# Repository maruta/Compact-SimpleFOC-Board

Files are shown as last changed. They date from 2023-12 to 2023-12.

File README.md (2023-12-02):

# Compact SimpleFOC Controller Board

This repository contains design data for a BLDC motor controller board composed of:

* RP2040 (Controller)
* TMC6300 (Driver)
* MT6535 (Magnetic Angle Sensor)
* INA240 (Current Sense Amplifier)

and mainly designed for a tiny inverted pendulm project.

Wheeled inverted pendulum powered by SimpleFOC-1080p60H mov (https://youtu.be/5sXEKwi0VvQ?si=sFahMU4BhdU_3RiM)

## Disclaimer

The information and design files in this repository are provided "as is" without warranty of any kind, express or implied. We make no guarantees regarding the functionality or reliability of these designs. Users assume full responsibility for the application and use of these files. Any commercial application of these designs is at the user's own risk.

## Description

The board is designed primarily for the SimpleFOC library, with an emphasis on easy customization of the software to suit your application.

The RP2040 component in this design is compatible with the Raspberry Pi Pico, minus the USB connector. It can be programmed using the Arduino IDE with the [Raspberry Pi Pico Arduino core](https://github.com/earlephilhower/arduino-pico), using the [Raspberry Pi Debug Probe](https://www.raspberrypi.com/products/debug-probe/).

### Board Specifications
- Voltage Range: 2-5.5 V
- Maximum Current: 2 A (1.4 Arms)

### Motor Compatibility
- The board has been tested with the RCTIMER GBM2804 motor.

### Connector Details

- J1: RP2040 SWD Connector (3-pin JST SH connector)
  - Pin 1: SWCLK
  - Pin 2: GND
  - Pin 3: SWDIO
- J2: Motor Connector (not populated; 2.54 mm)
  - Pin 1: Motor Phase U
  - Pin 2: Motor Phase V
  - Pin 3: Motor Phase W
- J3: Power and Interface Connector
  - 4-pin JST SH Connector
  - compatible with Qwiic
  - Logic voltage is 3.3 V
  - Pin assign
    - Pin 1: Ground (GND)
    - Pin 2: Positive Voltage (V+)
    - Pin 3: GPIO4 (I2C0 SDA / UART1_TX)
    - Pin 4: GPIO5 (I2C0 SCL / UART1_RX)

## Manufacturing

Use the `production` folder for manufacturing this board with [JLCPCB](https://jlcpcb.com/).

### JLCPCB Ordering Guide

PCB Manufacturing Specifications:
- File to Upload: `gerber.zip`
- Key Settings:
  - Via Covering: Epoxy Filled & Capped
  - Min. via hole size/diameter: 0.2mm(0.3/0.35mm)

PCB Assembly Details:
- Key Settings:
  - Assembly Side: Both Sides
  - Confirm Parts Placement: Required
  - Board Depaneling & Edge Rail: As per requirement
- Required Files: `BOM: bom.csv`, `CPL: positions.csv`
- Components not automatically selected are specified by LCSC part numbers in the circuit files.
- RT6150 and TMC6300 need to be ordered through Global Sourcing Parts Service due to their unavailability at JLCPCB. *Note that the quantity required may be more than the actual quantity to be implemented.*

## Circuit Editing

* Created using KiCAD v7.

* Component models from [Ultra Librarian](https://www.ultralibrarian.com/) are not included due to licensing. Download these models to edit the circuit. See README.md in the following folders for more information:

  - ul_RT6150B-33GQW
  - ul_TMC6300-LA
  - ul_W25Q16JVUXIQ

* Use [Fabrication Toolkit](https://github.com/bennymeg/JLC-Plugin-for-KiCad) to generate . Generated files are stored in the `production` folder.

## License

Files in this repository are under the MIT License.

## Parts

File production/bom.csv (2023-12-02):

Designator | Footprint | Quantity | Value | LCSC Part #
C1, C7, C9 | 0402 | 3 | 2u2
C10, C11, C12, C13, C14, C15, C17, C18, C19, C20, C22, C23, C24, C25, C6, C8 | 0201 | 16 | 100n
C16 | 0201 | 1 | 1n
C2 | 0805 | 1 | 47u
C21 | 1210 | 1 | 47u
C3 | 0805 | 1 | 22u
C4, C5 | 0201 | 2 | 15p
D1 | 0805 | 1 | LED Red | C84256
D2 | 0805 | 1 | LED Orange | C84262
D3 | D_SOD-123 | 1 | 6V
D4 | 0805 | 1 | LED Green | C84260
J1 | JST_SH_SM03B-SRSS-TB_1x03-1MP_P1.00mm_Horizontal | 1 | SM03B-SRSS-TB
J3 | JST_SH_BM04B-SRSS-TB_1x04-1MP_P1.00mm_Vertical | 1 | BM04B-SRSS-TB
L1 | L_Changjiang_FNR5020S | 1 | 2u2
Q1 | SOT-523 | 1 | DMG1012T
R1, R10, R11, R12, R4, R7, R8, R9 | 0402 | 8 | 100k
R13, R14, R15 | 0402 | 3 | 470
R16, R17, R6 | 0805 | 3 | 10m
R18, R2 | 0402 | 2 | 1k
R3 | 0402 | 1 | 330k
R5 | 0402 | 1 | 300
U1 | QFN-56-1EP_7x7mm_P0.4mm_EP3.2x3.2mm | 1 | RP2040
U2, U4, U5 | TSSOP-8_4.4x3mm_P0.65mm | 3 | INA240A2PWR
U3 | QFN20_3x3_TRI | 1 | TMC6300-LA-T
U6 | W25Q16JVUXIQ_WIN | 1 | W25Q16JVUXIQ
U7 | 10-WFDFN-EP_RIT-M | 1 | RT6150B-33GQW
U8 | SOT-23 | 1 | LM4040DBZ-3
U9 | TSSOP-16_4.4x5mm_P0.65mm | 1 | MT6835GT-STD
Y1 | Crystal_SMD_3225-4Pin_3.2x2.5mm | 1 | X322512MSB4SI

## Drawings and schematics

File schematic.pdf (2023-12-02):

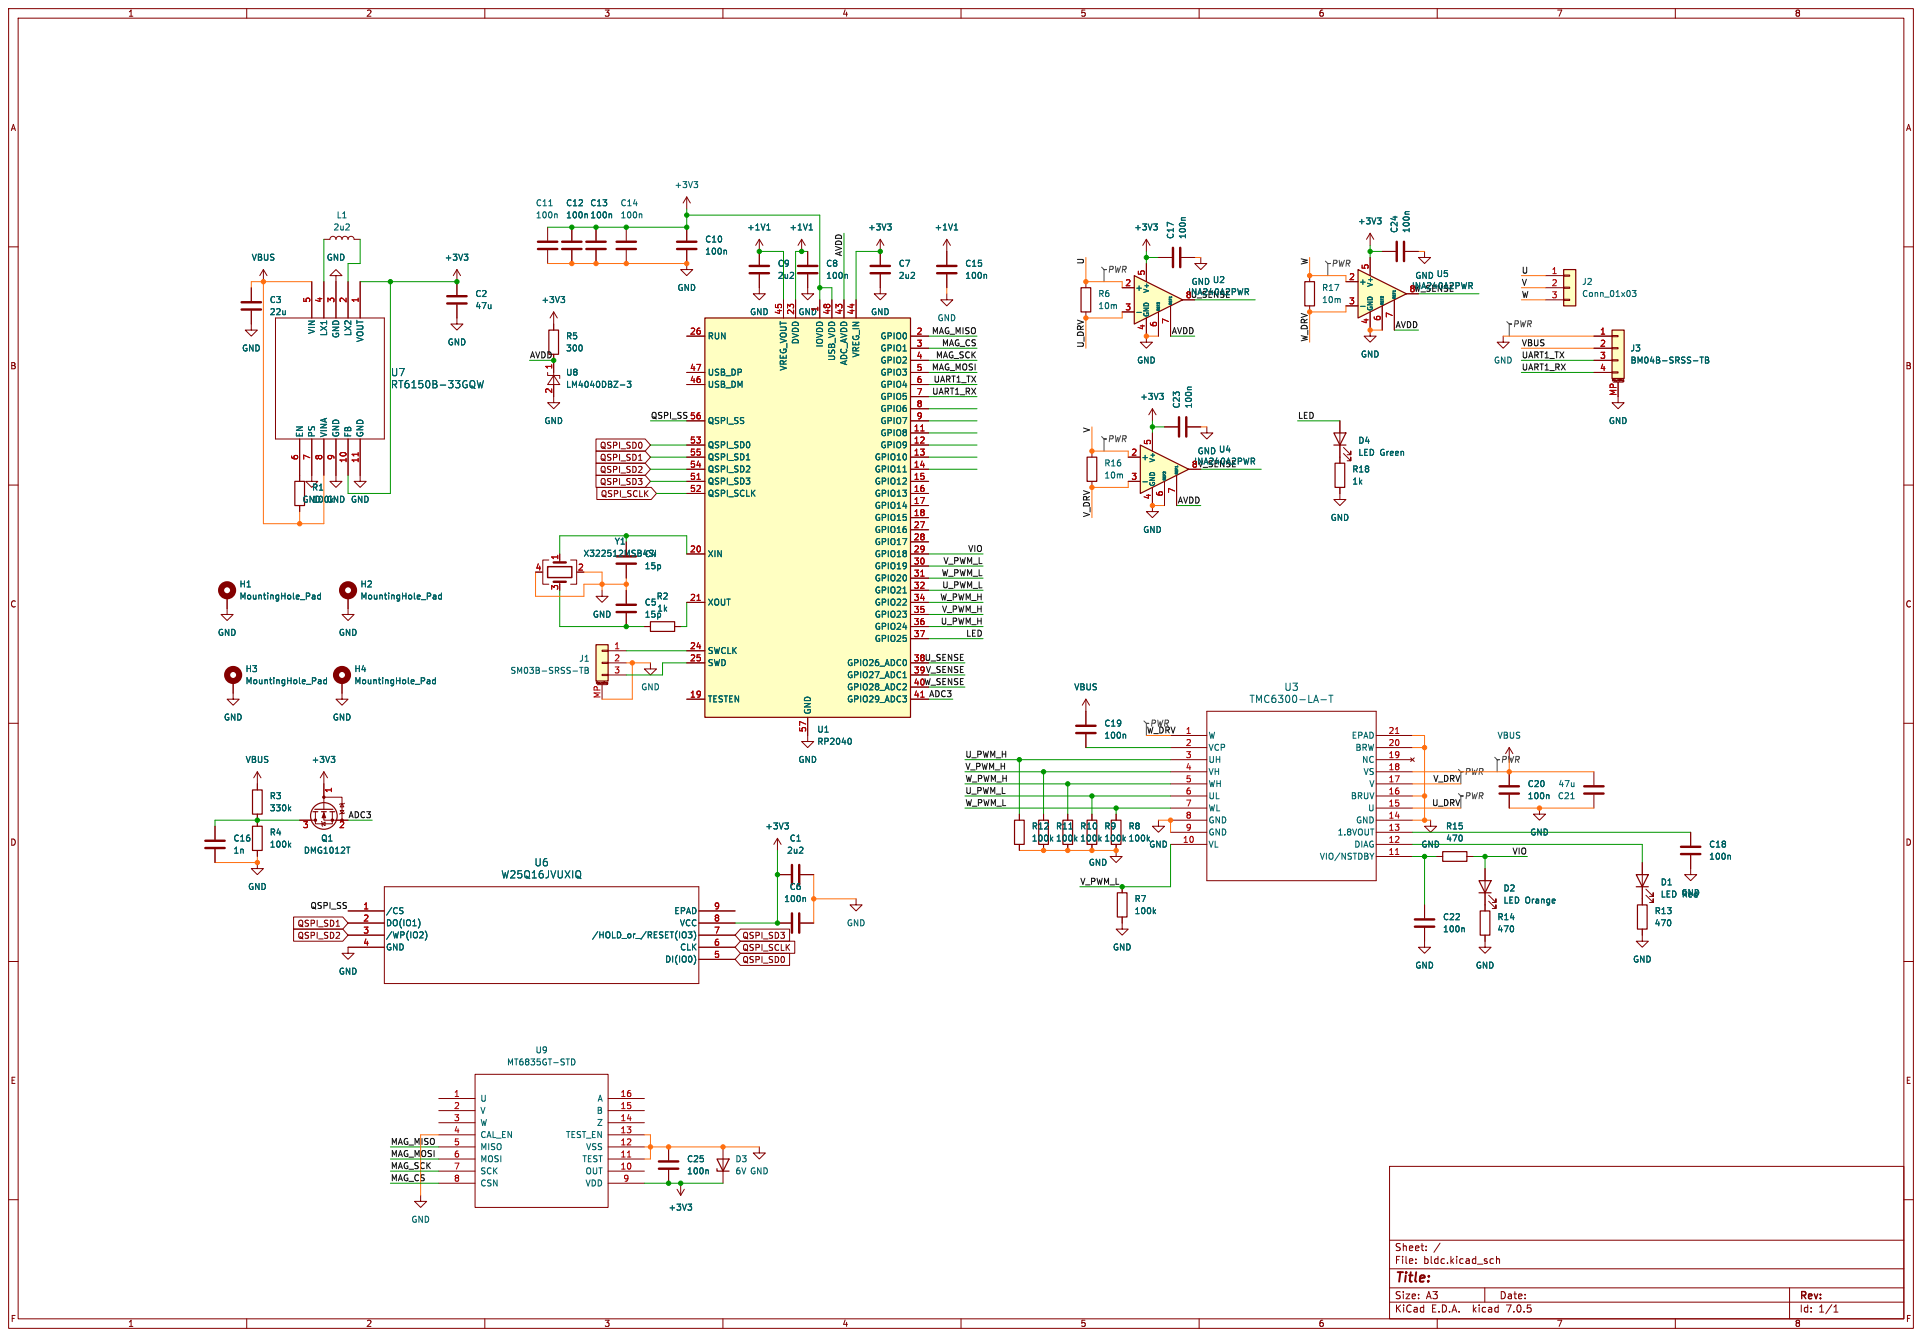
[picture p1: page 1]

1 GPIO8 11 GPIO9 12 GPIO10 13 GPIO11 14 GPIO12 15 GPIO13 16 GPIO14 17 GPIO15 18 TESTEN 19 GPIO0 2 XIN 20 XOUT 21 DVDD 23 SWCLK 24 SWD 25 RUN 26 GPIO16 27 GPIO17 28 GPIO18 29 GPIO1 3 GPIO19 30 GPIO20 31 GPIO21 32 GPIO22 34 GPIO23 35 GPIO24 36 GPIO25 37 GPIO26_ADC0 38 GPIO27_ADC1 39 GPIO2 4 GPIO28_ADC2 40 GPIO29_ADC3 41 ADC_AVDD 43 VREG_IN 44 VREG_VOUT 45 USB_DM 46 USB_DP 47 USB_VDD 48 GPIO3 5 QSPI_SD3 51 QSPI_SCLK 52 QSPI_SD0 53 QSPI_SD2 54 QSPI_SD1 55 QSPI_SS 56 GND 57 GPIO4 6 GPIO5 7 GPIO6 8 GPIO7 9 U1 RP2040

1 GPIO8 11 GPIO9 12 GPIO10 13 GPIO11 14 GPIO12 15 GPIO13 16 GPIO14 17 GPIO15 18 TESTEN 19 GPIO0 2 XIN 20 XOUT 21 DVDD 23 SWCLK 24 SWD 25 RUN 26 GPIO16 27 GPIO17 28 GPIO18 29 GPIO1 3 GPIO19 30 GPIO20 31 GPIO21 32 GPIO22 34 GPIO23 35 GPIO24 36 GPIO25 37 GPIO26_ADC0 38 GPIO27_ADC1 39 GPIO2 4 GPIO28_ADC2 40 GPIO29_ADC3 41 ADC_AVDD 43 VREG_IN 44 VREG_VOUT 45 USB_DM 46 USB_DP 47 USB_VDD 48 GPIO3 5 QSPI_SD3 51 QSPI_SCLK 52 QSPI_SD0 53 QSPI_SD2 54 QSPI_SD1 55 QSPI_SS 56 GND 57 GPIO4 6 GPIO5 7 GPIO6 8 GPIO7 9 GND GND

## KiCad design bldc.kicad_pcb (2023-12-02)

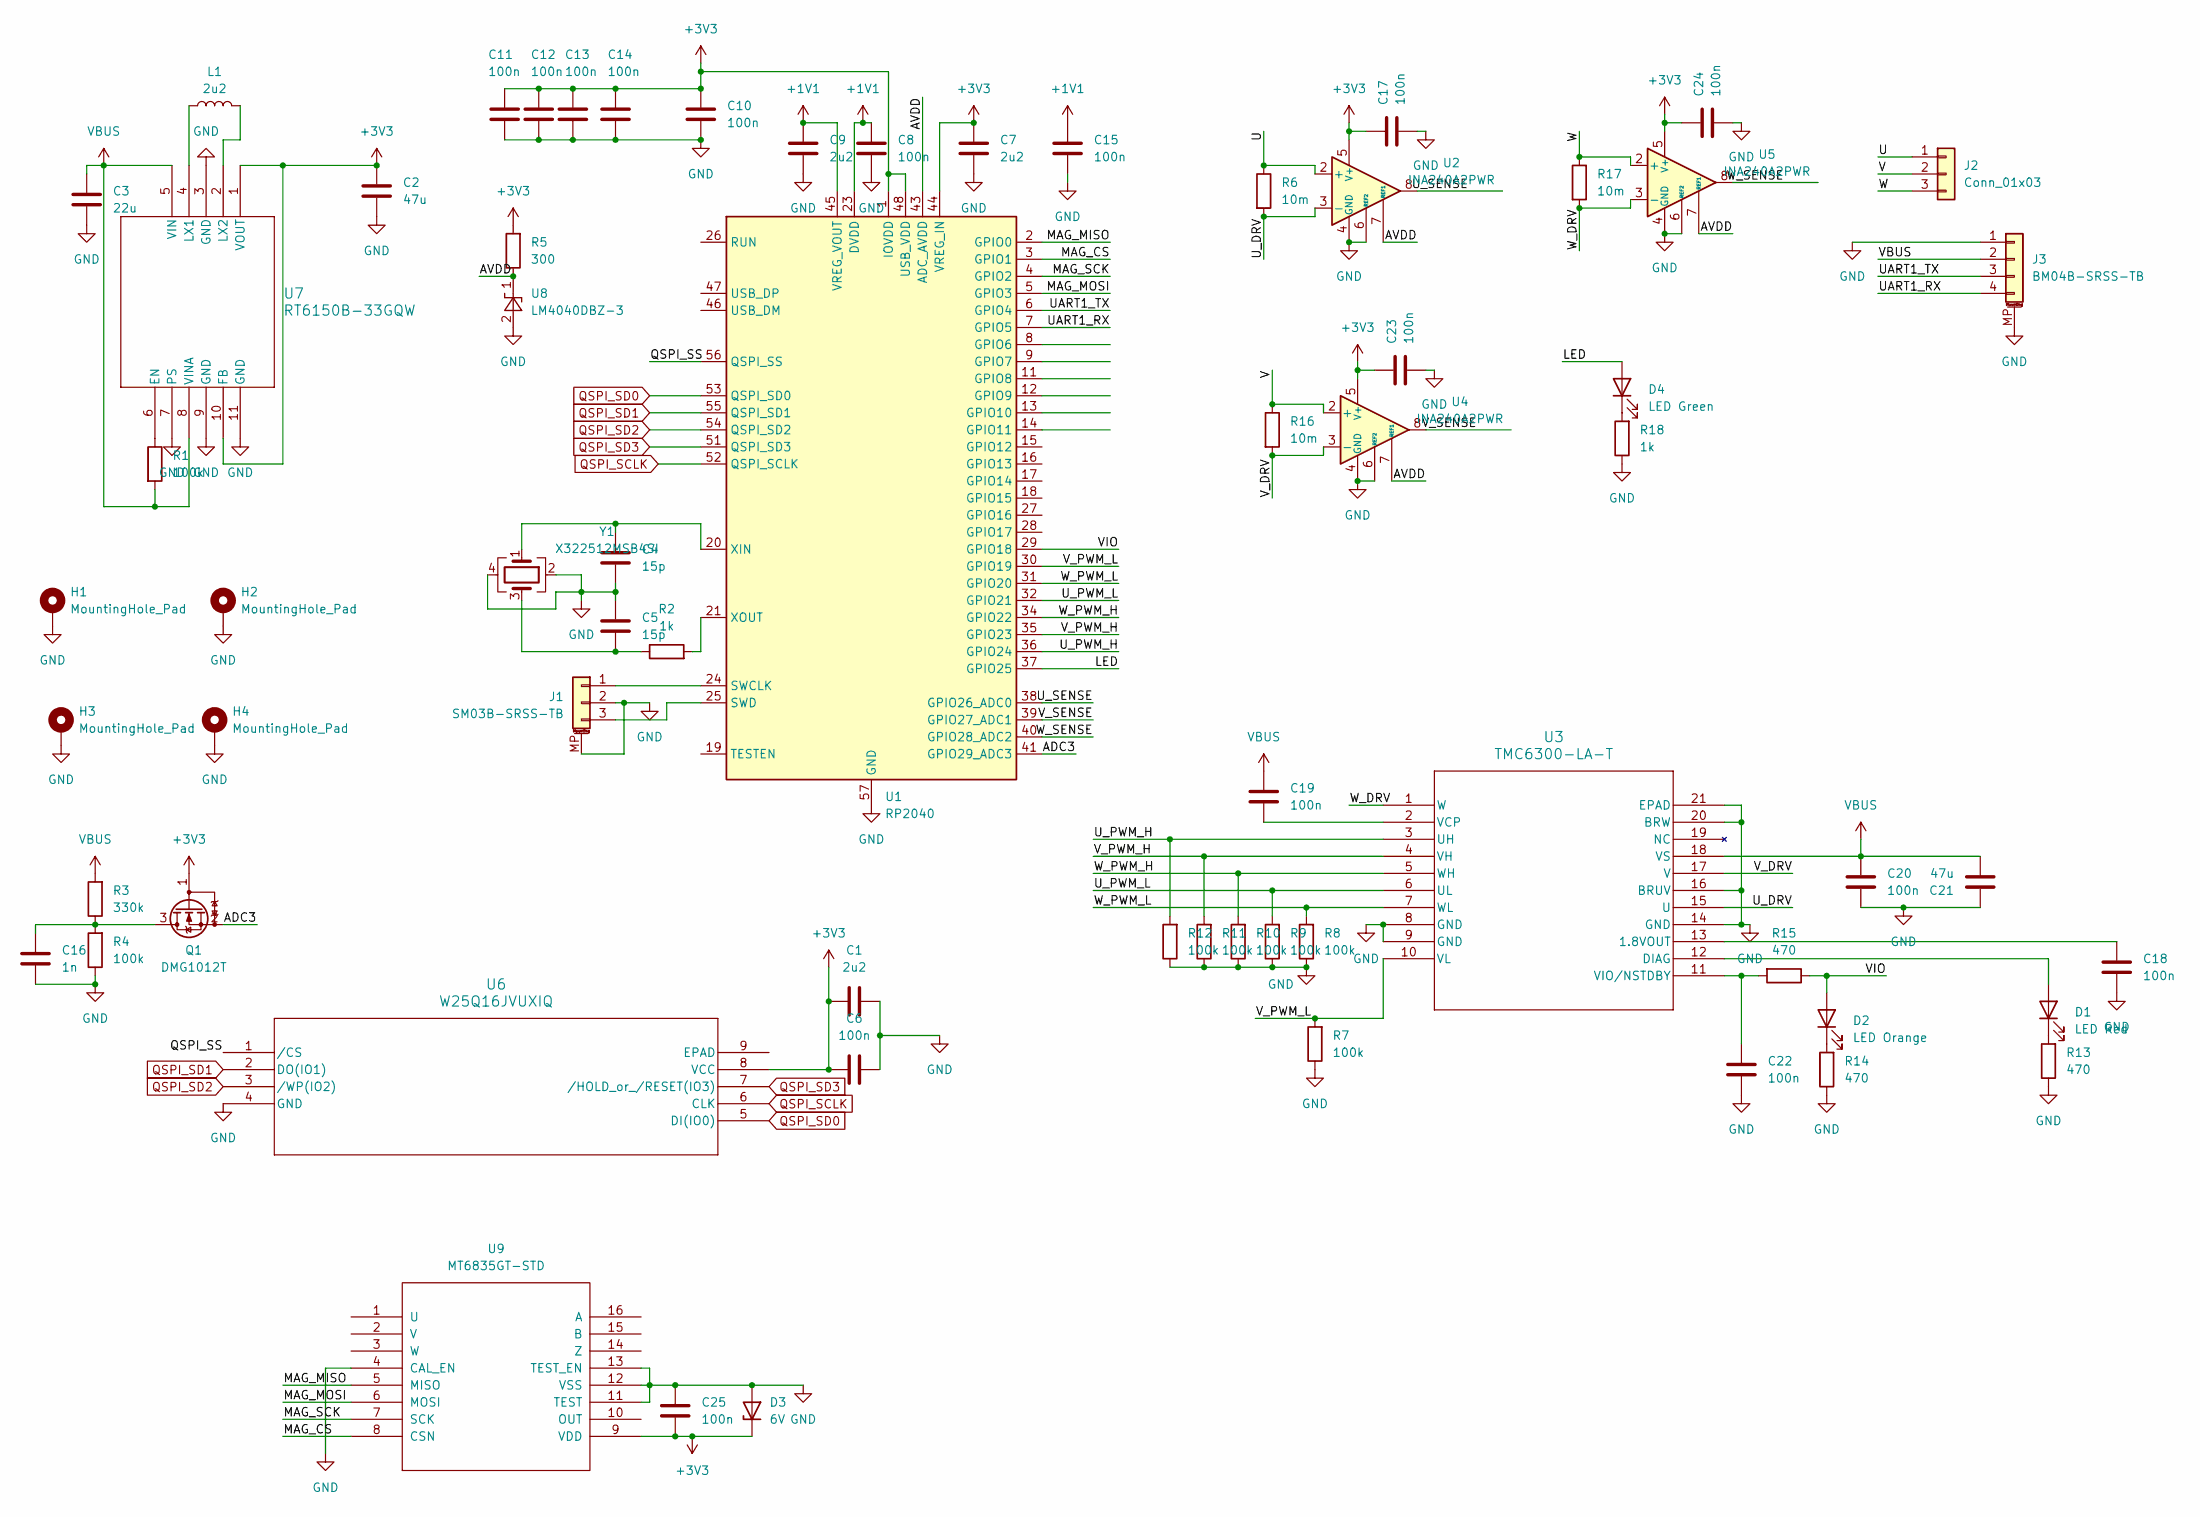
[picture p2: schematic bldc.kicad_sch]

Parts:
C1, C7, C9: 2u2; C_0402_1005Metric
C2: 47u; C_0805_2012Metric
C3: 22u; C_0805_2012Metric
C4, C5: 15p; C_0201_0603Metric
C6, C8, C10, C11, C12, C13, C14, C15, C17, C18, C19, C20, C22, C23, C24, C25: 100n; C_0201_0603Metric
C16: 1n; C_0201_0603Metric
C21: 47u; C_1210_3225Metric
D1: LED Red; LED_0805_2012Metric; LCSC C84256
D2: LED Orange; LED_0805_2012Metric; LCSC C84262
D3: 6V; D_SOD-123; JLCPCB Rotation Offset 180
D4: LED Green; LED_0805_2012Metric; LCSC C84260
H1, H2, H3, H4: MountingHole_Pad; MountingHole_2.2mm_M2_Pad_Via
J1: SM03B-SRSS-TB; JST_SH_SM03B-SRSS-TB_1x03-1MP_P1.00mm_Horizontal
J2: Conn_01x03; PinHeader_1x03_P2.54mm_Vertical
J3: BM04B-SRSS-TB; JST_SH_BM04B-SRSS-TB_1x04-1MP_P1.00mm_Vertical
L1: 2u2; L_Changjiang_FNR5020S
Q1: DMG1012T; SOT-523
R1, R4, R7, R8, R9, R10, R11, R12: 100k; R_0402_1005Metric
R2, R18: 1k; R_0402_1005Metric
R3: 330k; R_0402_1005Metric
R5: 300; R_0402_1005Metric
R6, R16, R17: 10m; R_0805_2012Metric
R13, R14, R15: 470; R_0402_1005Metric
U1: RP2040; QFN-56-1EP_7x7mm_P0.4mm_EP3.2x3.2mm
U2, U4, U5: INA240A2PWR; TSSOP-8_4.4x3mm_P0.65mm; JLCPCB Rotation Offset 90
U3: TMC6300-LA-T; QFN20_3x3_TRI
U6: W25Q16JVUXIQ; W25Q16JVUXIQ_WIN; JLCPCB Rotation Offset -90
U7: RT6150B-33GQW; 10-WFDFN-EP_RIT-M
U8: LM4040DBZ-3; SOT-23
U9: MT6835GT-STD; TSSOP-16_4.4x5mm_P0.65mm; JLCPCB Rotation Offset 90
Y1: X322512MSB4SI; Crystal_SMD_3225-4Pin_3.2x2.5mm

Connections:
+1V1: C8.2, C9.2, C15.2, U1.23 (DVDD), U1.45 (VREG_VOUT), U1.50 (DVDD)
+3V3: C1.1, C2.1, C6.1, C7.2, C10.2, C11.2, C12.2, C13.2, C14.2, C17.2, C23.2, C24.2, C25.1, D3.1 (K), Q1.1 (G), R5.2, U1.1 (IOVDD), U1.10 (IOVDD), U1.22 (IOVDD), U1.33 (IOVDD), U1.42 (IOVDD), U1.44 (VREG_IN), U1.48 (USB_VDD), U1.49 (IOVDD), U2.5 (V+), U4.5 (V+), U5.5 (V+), U6.8 (VCC), U7.1 (VOUT), U7.10 (FB), U9.9 (VDD)
/ADC3: Q1.2 (S), U1.41 (GPIO29_ADC3)
/AVDD: R5.1, U1.43 (ADC_AVDD), U2.7 (REF1), U4.7 (REF1), U5.7 (REF1), U8.1 (K)
/LED: D4.2 (A), U1.37 (GPIO25)
/MAG_CS: U1.3 (GPIO1), U9.8 (CSN)
/MAG_MISO: U1.2 (GPIO0), U9.5 (MISO)
/MAG_MOSI: U1.5 (GPIO3), U9.6 (MOSI)
/MAG_SCK: U1.4 (GPIO2), U9.7 (SCK)
/QSPI_SS: U1.56 (QSPI_SS), U6.1 (/CS)
/U: J2.1, R6.1, U2.2 (+)
/UART1_RX: J3.4, U1.7 (GPIO5)
/UART1_TX: J3.3, U1.6 (GPIO4)
/U_DRV: R6.2, U2.3 (-), U3.15 (U)
/U_PWM_H: R12.2, U1.36 (GPIO24), U3.3 (UH)
/U_PWM_L: R9.2, U1.32 (GPIO21), U3.6 (UL)
/U_SENSE: U1.38 (GPIO26_ADC0), U2.8
/V: J2.2, R16.1, U4.2 (+)
/VIO: D2.2 (A), R15.1, U1.29 (GPIO18)
/V_DRV: R16.2, U3.17 (V), U4.3 (-)
/V_PWM_H: R11.2, U1.35 (GPIO23), U3.4 (VH)
/V_PWM_L: R7.2, U1.30 (GPIO19), U3.10 (VL)
/V_SENSE: U1.39 (GPIO27_ADC1), U4.8
/W: J2.3, R17.1, U5.2 (+)
/W_DRV: R17.2, U3.1 (W), U5.3 (-)
/W_PWM_H: R10.2, U1.34 (GPIO22), U3.5 (WH)
/W_PWM_L: R8.2, U1.31 (GPIO20), U3.7 (WL)
/W_SENSE: U1.40 (GPIO28_ADC2), U5.8
GND: C1.2, C2.2, C3.2, C4.2, C5.1, C6.2, C7.1, C8.1, C9.1, C10.1, C11.1, C12.1, C13.1, C14.1, C15.1, C16.1, C17.1, C18.1, C20.1, C21.2, C22.1, C23.1, C24.1, C25.2, D3.2 (A), H1.1, H2.1, H3.1, H4.1, J1.2, J1.MP (MountPin), J3.1, J3.MP (MountPin), R4.1, R7.1, R8.1, R9.1, R10.1, R11.1, R12.1, R13.1, R14.1, R18.1, U1.57 (GND), U2.1 (GND), U2.4 (GND), U2.6 (REF2), U3.8 (GND), U3.9 (GND), U3.14 (GND), U3.16 (BRUV), U3.20 (BRW), U3.21 (EPAD), U4.1 (GND), U4.4 (GND), U4.6 (REF2), U5.1 (GND), U5.4 (GND), U5.6 (REF2), U6.4 (GND), U7.3 (GND), U7.7 (PS), U7.9 (GND), U7.11 (GND), U8.2 (A), U9.4 (CAL_EN), U9.11 (TEST), U9.12 (VSS), U9.13 (TEST_EN), Y1.2, Y1.4
unnamed: C5.2, R2.1, Y1.3
unnamed: D1.2 (A), U3.12 (DIAG)
unnamed: D1.1 (K), R13.2
unnamed: D2.1 (K), R14.2
unnamed: D4.1 (K), R18.2
unnamed: J1.1, U1.24 (SWCLK)
unnamed: J1.3, U1.25 (SWD)
unnamed: C16.2, Q1.3 (D), R3.1, R4.2
unnamed: C4.1, U1.20 (XIN), Y1.1
unnamed: R2.2, U1.21 (XOUT)
unnamed: C18.2, U3.13 (1.8VOUT)
unnamed: C19.1, U3.2 (VCP)
unnamed: C22.2, R15.2, U3.11 (VIO/NSTDBY)
unnamed: R1.1, U7.6 (EN)
unnamed: L1.1, U7.4 (LX1)
unnamed: L1.2, U7.2 (LX2)
QSPI_SCLK: U1.52 (QSPI_SCLK), U6.6 (CLK)
QSPI_SD0: U1.53 (QSPI_SD0), U6.5 (DI(IO0))
QSPI_SD1: U1.55 (QSPI_SD1), U6.2 (DO(IO1))
QSPI_SD2: U1.54 (QSPI_SD2), U6.3 (/WP(IO2))
QSPI_SD3: U1.51 (QSPI_SD3), U6.7 (/HOLD_or_/RESET(IO3))
VBUS: C3.1, C19.2, C20.2, C21.1, J3.2, R1.2, R3.2, U3.18 (VS), U7.5 (VIN), U7.8 (VINA)

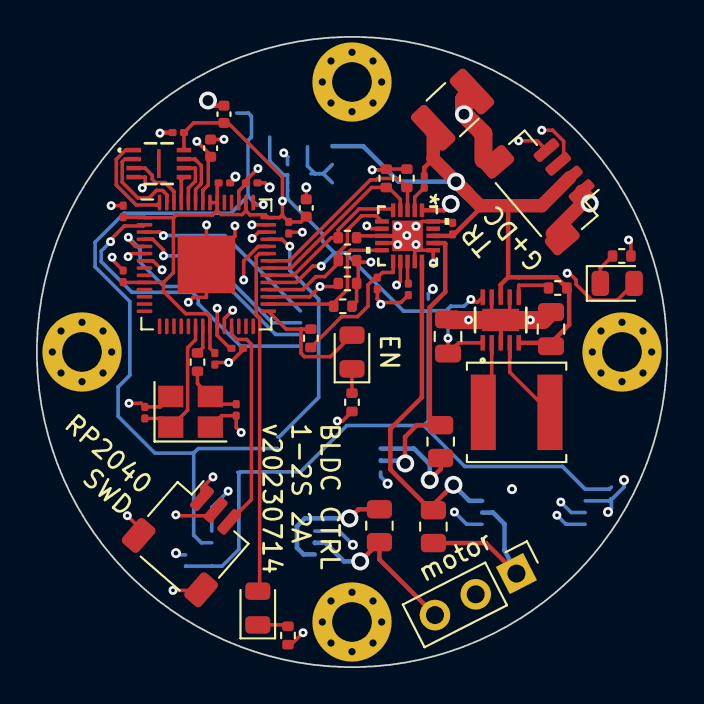
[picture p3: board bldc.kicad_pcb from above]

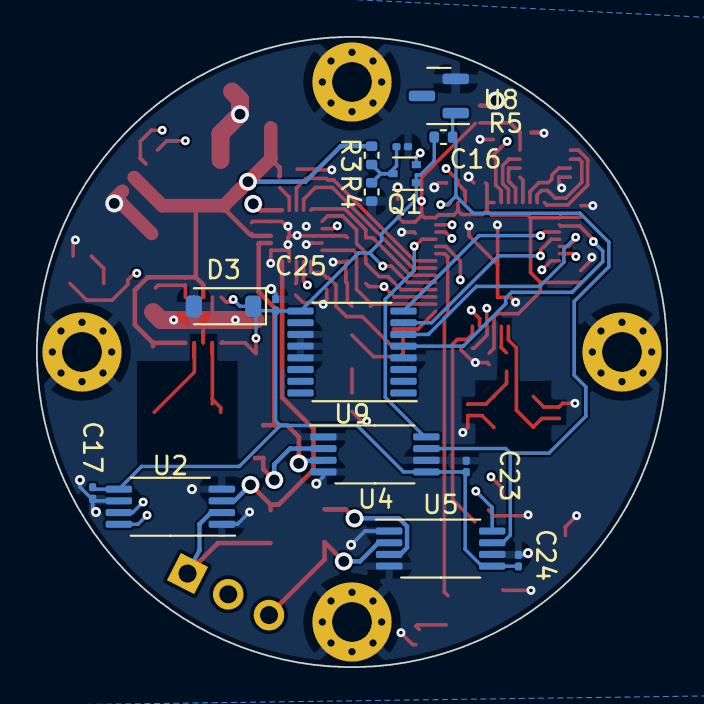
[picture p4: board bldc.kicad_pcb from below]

Board: 4 copper layers, 35.0 x 35.0 mm, 66 parts (15 on the bottom side), 51 nets.

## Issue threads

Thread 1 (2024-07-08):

[question]   Torque control in foc_current/torque.

freemanzwin, 2024-07-08:
( sorry for poor English)
Thank you for the resource.
I have a question while studying.

You used foc_current/torque...
If I use your PID settings below, I can't control the torque like in the video, is it the right PID setting?

  // current q loop PID
  motor.PID_current_q.P = 5.0;
  motor.PID_current_q.I = 5000.0;
  motor.PID_current_q.D = 0.0;
  motor.PID_current_q.output_ramp = 0.0;
  motor.PID_current_q.limit = 5.0;
  // Low pass filtering time constant
  motor.LPF_current_q.Tf = 0.005;
  // current d loop PID
  motor.PID_current_d.P = 5.0;
  motor.PID_current_d.I = 5000.0;
  motor.PID_current_d.D = 0.0;
  motor.PID_current_d.output_ramp = 0.0;
  motor.PID_current_d.limit = 5.0;
  motor.LPF_current_d.Tf = 0.005;

maruta, 2024-07-15:
Without knowing the specific circumstances of the failure, it is difficult to say anything about the gain adjustment, but the video uses a velocity control loop.

Closed 2024-08-04.

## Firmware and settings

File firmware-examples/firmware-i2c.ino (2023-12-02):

// Require SimpleFOC library and SimpleFOCDrivers library

// this setting seems not working :(
#define SIMPLEFOC_RP2040_ADC_VDDA 3.0f

#include <SimpleFOC.h>
#include "SimpleFOCDrivers.h"

#include "encoders/mt6835/MagneticSensorMT6835.h"
#include <EEPROM.h>

const float voltage_power_supply = 5.0;
const float current_limit = 0.5;

// Intended to be used for robots with motors on both sides
const uint8_t I2C_ADDR = 0x24; // LEFT
//const uint8_t I2C_ADDR = 0x25;  // RIGHT
const int I2C_CLOCK = 1000000;

SPISettings myMT6835SPISettings(1000000, MT6835_BITORDER, SPI_MODE3);
MagneticSensorMT6835 sensor = MagneticSensorMT6835(1, myMT6835SPISettings);

InlineCurrentSense current_sense = InlineCurrentSense(0.01f, -50.0f, A0, A2, A1);

// BLDC motor & driver instance
BLDCMotor motor = BLDCMotor(7, 10.0, 145.0 * 30 / 3.1415);
BLDCDriver6PWM driver = BLDCDriver6PWM(24, 21, 22, 20, 23, 19, 18);


struct MotorState {
  float angle;
  float velocity;
};

struct CalibData {
  char mark[5];
  float zero_electric_angle;
  Direction sensor_direction;
};

void readFromEEPROM(int startAddress, CalibData& data) {
  byte* dataPointer = (byte*)(void*)&data;
  for (size_t i = 0; i < sizeof(CalibData); ++i) {
    dataPointer[i] = EEPROM.read(startAddress + i);
  }
}


void setup() {
  // load calibration data from EEPROM if available
  EEPROM.begin(512);
  CalibData caldat;
  readFromEEPROM(0, caldat);
  if (caldat.mark[0] == 'd' && caldat.mark[1] == 'o' && caldat.mark[2] == 'n' && caldat.mark[3] == 'e') {
    motor.zero_electric_angle = caldat.zero_electric_angle;
    motor.sensor_direction = caldat.sensor_direction;
  }

  // initialise magnetic sensor hardware
  SPI.setRX(0);
  SPI.setCS(1);
  SPI.setTX(3);
  SPI.setSCK(2);
  sensor.init();
  sensor.setZeroPosition(0);

  // link the motor to the sensor
  motor.linkSensor(&sensor);
  motor.sensor_direction = Direction::CW;

  // driver config
  // power supply voltage [V]
  driver.voltage_power_supply = voltage_power_supply;
  driver.init();
  // link driver
  motor.linkDriver(&driver);
  current_sense.linkDriver(&driver);
  current_sense.skip_align = true;
  // control loop type and torque mode
  motor.torque_controller = TorqueControlType::foc_current;
  motor.controller = MotionControlType::torque;
  motor.motion_downsample = 0.0;

  // velocity loop PID
  motor.PID_velocity.P = 0.5;
  motor.PID_velocity.I = 10.0;
  motor.PID_velocity.D = 0.0;
  motor.PID_velocity.output_ramp = 1000.0;
  motor.PID_velocity.limit = 0.5;
  // Low pass filtering time constant
  motor.LPF_velocity.Tf = 0.05;
  // angle loop PID (not tuned)
  motor.P_angle.P = 30.0;
  motor.P_angle.I = 0.0;
  motor.P_angle.D = 0.0;
  motor.P_angle.output_ramp = 0.0;
  motor.P_angle.limit = 100.0;
  // Low pass filtering time constant
  motor.LPF_angle.Tf = 0.0;
  // current q loop PID
  motor.PID_current_q.P = 5.0;
  motor.PID_current_q.I = 5000.0;
  motor.PID_current_q.D = 0.0;
  motor.PID_current_q.output_ramp = 0.0;
  motor.PID_current_q.limit = 5.0;
  // Low pass filtering time constant
  motor.LPF_current_q.Tf = 0.005;
  // current d loop PID
  motor.PID_current_d.P = 5.0;
  motor.PID_current_d.I = 5000.0;
  motor.PID_current_d.D = 0.0;
  motor.PID_current_d.output_ramp = 0.0;
  motor.PID_current_d.limit = 5.0;
  // Low pass filtering time constant
  motor.LPF_current_d.Tf = 0.005;
  // Limits
  motor.velocity_limit = 100.0;
  motor.voltage_limit = voltage_power_supply;
  motor.current_limit = current_limit;

  motor.foc_modulation = FOCModulationType::SpaceVectorPWM;

  // initialise motor
  motor.init();
  current_sense.init();
  motor.linkCurrentSense(&current_sense);

  motor.monitor_variables = 0;

  // If both motors perform calibration operations at the same time, 
  // excessive current will flow, so a time difference is needed.
  if (I2C_ADDR == 0x25) {
    _delay(500);
  }

  motor.initFOC();


  motor.disable();

  _delay(10);

  Wire.setSDA(4);
  Wire.setSCL(5);

  Wire.setClock(I2C_CLOCK);
  Wire.begin(I2C_ADDR);
  Wire.onRequest(requestEvent);
  Wire.onReceive(receiveEvent);
}

void requestEvent() {
  MotorState dataToSend;
  dataToSend.angle = sensor.getAngle();
  dataToSend.velocity = sensor.getVelocity();
  byte* bytePtr = (byte*)(&dataToSend);
  for (int i = 0; i < sizeof(MotorState); i++) {
    Wire.write(*bytePtr++);
  }
}

inline void parseTorqueCommand() {
  motor.controller = MotionControlType::torque;
  setTargetFromI2C();
}

inline void parseVelocityCommand() {
  motor.controller = MotionControlType::velocity;
  setTargetFromI2C();
}

inline void parseAngleCommand() {
  motor.controller = MotionControlType::angle;
  setTargetFromI2C();
}

void receiveEvent(int numBytes) {
  if (numBytes <= 0) return;

  uint8_t registerAddress = Wire.read();

  switch (registerAddress) {
    case 0x00:
      parseEnableCommand();
      break;

    case 0x01:
      parseTorqueCommand();
      break;

    case 0x02:
      parseVelocityCommand();
      break;

    case 0x04:
      parseAngleCommand();

    default:
      break;
  }
}

inline void setTargetFromI2C() {
  if (Wire.available() == sizeof(float)) {
    union {
      float asFloat;
      uint8_t asBytes[sizeof(float)];
    } dataUnion;

    for (unsigned int i = 0; i < sizeof(float); i++) {
      dataUnion.asBytes[i] = Wire.read();
    }
    motor.target = dataUnion.asFloat;
  }
}

inline void parseEnableCommand() {
  if (Wire.available() == sizeof(uint8_t)) {
    uint8_t cmd = Wire.read();
    if (cmd == 1) {
      motor.target = 0;
      motor.enable();
    } else {
      motor.disable();
    }
  }
}

void loop() {
  motor.loopFOC();
  motor.move();
}

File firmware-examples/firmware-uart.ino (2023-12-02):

/*
 This code uses J4 as a UART and provide Commander interface.
 
 Also performs calibration of the sensors and write to EEPROM.
*/

// this setting seems not working :(
#define SIMPLEFOC_RP2040_ADC_VDDA 3.0f

#include <SimpleFOC.h>
#include <EEPROM.h>

#include "SimpleFOCDrivers.h"

#include "encoders/mt6835/MagneticSensorMT6835.h"


SPISettings myMT6835SPISettings(1000000, MT6835_BITORDER, SPI_MODE3);
MagneticSensorMT6835 sensor = MagneticSensorMT6835(1, myMT6835SPISettings);

InlineCurrentSense current_sense = InlineCurrentSense(0.01f, -50.0f, A0, A2, A1);

// BLDC motor & driver instance
BLDCMotor motor = BLDCMotor(7, 10.0f, 145.0f * 30.0f / _PI);
BLDCDriver6PWM driver = BLDCDriver6PWM(24, 21, 22, 20, 23, 19, 18);

float target_voltage = 5;
struct CalibData {
  char mark[5];
  float zero_electric_angle;
  Direction sensor_direction;
};

void writeToEEPROM(int startAddress, const CalibData& data) {
  const byte* dataPointer = (const byte*)(const void*)&data;
  for (size_t i = 0; i < sizeof(CalibData); ++i) {
    EEPROM.write(startAddress + i, dataPointer[i]);
  }
}

void readFromEEPROM(int startAddress, CalibData& data) {
  byte* dataPointer = (byte*)(void*)&data;
  for (size_t i = 0; i < sizeof(CalibData); ++i) {
    dataPointer[i] = EEPROM.read(startAddress + i);
  }
}

// commander interface
Commander command = Commander(Serial2);
void onMotor(char* cmd) {
  command.motor(&motor, cmd);
}
void doTarget(char* cmd) {
  command.scalar(&target_voltage, cmd);
}
void calcKV(char* cmd) {
  Serial2.println(motor.shaft_velocity / motor.target * 30.0f / _PI);
}

void setup() {
  EEPROM.begin(512);
  // initialise magnetic sensor hardware
  SPI.setRX(0);
  SPI.setCS(1);
  SPI.setTX(3);
  SPI.setSCK(2);
  sensor.init();
  // link the motor to the sensor
  motor.linkSensor(&sensor);
  motor.sensor_direction = Direction::CW;
  // driver config
  // power supply voltage [V]
  driver.voltage_power_supply = 5.0;
  driver.init();
  // link driver
  motor.linkDriver(&driver);
  current_sense.linkDriver(&driver);

  // control loop type and torque mode
  motor.torque_controller = TorqueControlType::foc_current;
  motor.controller = MotionControlType::torque;
  motor.motion_downsample = 0.0;

  // velocity loop PID
  motor.PID_velocity.P = 0.5;
  motor.PID_velocity.I = 10.0;
  motor.PID_velocity.D = 0.0;
  motor.PID_velocity.output_ramp = 1000.0;
  motor.PID_velocity.limit = 0.5;
  // Low pass filtering time constant
  motor.LPF_velocity.Tf = 0.05;
  // angle loop PID (not tuned)
  motor.P_angle.P = 30.0;
  motor.P_angle.I = 0.0;
  motor.P_angle.D = 0.0;
  motor.P_angle.output_ramp = 0.0;
  motor.P_angle.limit = 100.0;
  // Low pass filtering time constant
  motor.LPF_angle.Tf = 0.0;
  // current q loop PID
  motor.PID_current_q.P = 5.0;
  motor.PID_current_q.I = 5000.0;
  motor.PID_current_q.D = 0.0;
  motor.PID_current_q.output_ramp = 0.0;
  motor.PID_current_q.limit = 5.0;
  // Low pass filtering time constant
  motor.LPF_current_q.Tf = 0.005;
  // current d loop PID
  motor.PID_current_d.P = 5.0;
  motor.PID_current_d.I = 5000.0;
  motor.PID_current_d.D = 0.0;
  motor.PID_current_d.output_ramp = 0.0;
  motor.PID_current_d.limit = 5.0;
  // Low pass filtering time constant
  motor.LPF_current_d.Tf = 0.005;
  // Limits
  motor.velocity_limit = 100.0;
  motor.voltage_limit = 5.0;
  motor.current_limit = 0.5;

  motor.foc_modulation = FOCModulationType::SpaceVectorPWM;

  // use monitoring with serial for motor init
  // monitoring port
  Serial2.setTX(4);
  Serial2.setRX(5);
  Serial2.begin(250000);
  // comment out if not needed
  motor.useMonitoring(Serial2);

  // initialise motor
  motor.init();


  motor.linkCurrentSense(&current_sense);
  current_sense.init();

  Serial2.print("current_sense.gain:\t");
  Serial2.print(current_sense.gain_a);
  Serial2.print(", ");
  Serial2.print(current_sense.gain_b);
  Serial2.print(", ");
  Serial2.println(current_sense.gain_c);
  Serial2.print("current_sense.offset_i:\t");
  Serial2.print(current_sense.offset_ia);
  Serial2.print(", ");
  Serial2.print(current_sense.offset_ib);
  Serial2.print(", ");
  Serial2.println(current_sense.offset_ic);

  motor.voltage_sensor_align = motor.voltage_limit;

  sensor.setZeroPosition(0);

  uint8_t st = sensor.getStatus();
  Serial2.print("MT6835: status = ");
  Serial2.println(st);


  uint16_t pos = sensor.getZeroPosition();
  Serial2.print("MT6835: zero position = ");
  Serial2.println(pos);



  // align encoder and start FOC
  motor.initFOC();

  Serial2.print("current_sense.gain:\t");
  Serial2.print(current_sense.gain_a);
  Serial2.print(", ");
  Serial2.print(current_sense.gain_b);
  Serial2.print(", ");
  Serial2.println(current_sense.gain_c);
  Serial2.print("current_sense.offset_i:\t");
  Serial2.print(current_sense.offset_ia);
  Serial2.print(", ");
  Serial2.print(current_sense.offset_ib);
  Serial2.print(", ");
  Serial2.println(current_sense.offset_ic);

  CalibData caldat = { "done", motor.zero_electric_angle, motor.sensor_direction };
  writeToEEPROM(0, caldat);
  EEPROM.commit();

  CalibData dataToRead;
  readFromEEPROM(0, dataToRead);
  EEPROM.end();
  Serial2.println(dataToRead.mark);
  Serial2.println(dataToRead.zero_electric_angle, 4);
  Serial2.println(dataToRead.sensor_direction == Direction::CW ? "Direction::CW" : "Direction::CCW");
  // set the inital target value
  motor.target = 0;

  // define the motor id
  command.add('A', onMotor, "motor");
  command.add('T', doTarget, "target voltage");
  command.add('K', calcKV, "calculate KV rating");

  // Run user commands to configure and the motor (find the full command list in docs.simplefoc.com)
  motor.monitor_variables = 0;
  _delay(1000);
}


void loop() {
  motor.loopFOC();

  motor.move();
  motor.monitor();
  command.run();
}
